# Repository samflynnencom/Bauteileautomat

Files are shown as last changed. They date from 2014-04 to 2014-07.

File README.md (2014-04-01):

Bauteileautomat
===============

This project merges the three branches of the student project "Bauteileautomat", a component vending machine built by students of the university of applied sciences Karlsruhe.
We all know the problem of working on a specific project and suddenly you encounter a missing part. And often it is a pretty common part like a 47k resistor you forgot to restock. That's where our vending machine comes into play. the machine holds the most common components and offers them to the students on the cheap.

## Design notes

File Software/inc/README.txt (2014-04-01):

Die includes sind in zwei Ordner aufgeteilt:

Im Ordner "driverlib" befinden sich alle Definitionen, die benötigt werden, wenn man die TivaWare nutzt. Dort befinden sich auch einige Konstanten. Diese Konstanten benötigt man, wenn man eine Applikation entwickelt. Später kann man ein eigenes Includefile schreiben, in dem die gesamten Konstanten selbst definiert werden können (muss aber nicht).
----
Im Ordner "hardware" befinden sich alle Includes, die man benötigt um die Hardware auf dem Chip selbst anzusprechen. Das bedeutet, wenn man den ADC nutzen möchte, dann benötigt man die Datei hw_adc.h dazu.
---

Normalerweise liefern die Dateien im Ordner "driverlib" die Konstanten wie auch Funktionsprototypen und die im Ordner "hardware" liegenden Includes die Definitionen zur eigentlichen Hardware. Die Tiva CPUs haben allerdings auch die Möglichkeit, die TivaWare, die in ihrem ROM steckt direkt zu nutzen. Dafür muss man vor alle Funktionen der TivaWare ein "ROM_" setzen und die include "rom.h" aus dem Ordner "driverlib" einbinden. Damit kann man allerdings ausschließlich Libraryfunktionen aus dem ROM nutzen. Wenn man sowohl Funktionen im Flash als auch im ROM nutzen möchte (zum Beispiel beim entwickeln), dann sollte man zusätzlich noch die Datei "rom_map.h" einbinden, die die Funktionen, die man als ROM_ nutzt, ersatzweise auf die Funktionen im Flash mappt.

Grundsätzlich gilt: Will man hardware ansprechen, bindet man die entsprechende hw_* aus dem Ordner "hardware" ein und sollte auch die entsprechende Funktion aus der Driverlib einbinden, gegen die man später linkt.

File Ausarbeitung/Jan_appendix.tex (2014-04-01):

\section{Anhang Elektronik}

\begin{figure}[h]

\hspace{-54pt}
\caption{Schemazeichnung des Mikrocontrollers mit Pinbelegung, JTAG Header und Takterzeugung. }
\label{SchemMic}
\end{figure}

\begin{figure}[h]

\hspace{-54pt}
\caption{Schemazeichnung der Netzwerkanbindung mit Koppeltrafo}
\label{SchemNetwork}
\end{figure}

\begin{figure}[h]

\hspace{-54pt}
\caption{Schemazeichnung der Motortreiber in der Daisychain}
\label{SchemMotor}
\end{figure}

\begin{figure}[h]

\hspace{-54pt}
\caption{Schemazeichnung der Motortreiber in der Daisychain}
\label{Board}
\end{figure}

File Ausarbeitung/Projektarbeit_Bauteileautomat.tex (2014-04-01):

\documentclass{scrartcl}
\usepackage[utf8]{inputenc}
\usepackage[german]{babel} 
\usepackage[colorlinks=true,
        linkcolor=black,
        citecolor=black,
        filecolor=black,
        urlcolor=black,
        bookmarks=true,
        bookmarksopen=true,
        bookmarksopenlevel=3,
        plainpages=false,
        pdfpagelabels=true]{hyperref}
\usepackage[square, numbers]{natbib}
\usepackage{setspace}
\usepackage[a4paper,left=2cm,right=2cm,top=2cm,bottom=4cm]{geometry}
\usepackage{graphicx}
\usepackage{morefloats}
\usepackage{ulem}
\usepackage{units}
\usepackage{wrapfig}
\usepackage{amsmath}
\usepackage{tikz}
\usepackage{colortbl} %Matze
\usepackage{xcolor}		%Matze 
\usepackage{pdfpages} %Matze
\usepackage{picinpar} %Matze
\definecolor{hellblau}{rgb}{0.8,0.8,1}
\definecolor {hellgruen}{rgb}{0.5,1,0.8}
%\usepackage{minted}
\usepackage[section]{placeins}
\usepackage{listingsutf8}
%\usepackage{wrapfig}
%\usepackage{pdfpages}
%\nocite{*}

\lstdefinestyle{customc}{
  belowcaptionskip=1\baselineskip,
  breaklines=true,
  frame=L,
  xleftmargin=\parindent,
  language=C,
  showstringspaces=false,
  basicstyle=\footnotesize\ttfamily,
  keywordstyle=\bfseries\color{green!40!black},
  commentstyle=\itshape\color{purple!40!black},
  identifierstyle=\color{blue},
  stringstyle=\color{orange},
}

\lstset{escapechar=@,style=customc, extendedchars=\true,
    inputencoding=utf8/latin1}

\parindent0mm

\newcommand {\Ohm} {$\Omega\ $}

\bibliographystyle{alphadin}

\begin{document}
\title{Projektarbeit 'Bauteileautomat'}
\author{
	Jan Krüger  \\
	Friedrichstraße 24 \\
	75417 Mühlacker \\
	Mtkl Nr: 37032 \\
	\and 
	Gregor Süß \\
	August-Dürr Straße 9 \\
	76133 Karlsruhe \\
	Mtkl Nr: 36496 \\
	\and
	Matthias Weißhaar \\
	Strümpfelbacher Straße 184\\
	71384 Weinstadt\\
	Mtkl Nr: 30250\\
	}

\date{\today}

\maketitle
\newpage

\tableofcontents
\newpage
\onehalfspace
\section{Einführung}
\subsection{Aufgabenstellung}
Für die Bereitstellung von elektronischen Bauteilen für die Studierenden der Elektrotechnik ist ein Ausgabeautomat zu entwickelen und zu erstellen. Der Automat ermöglicht den Studenten der Fakultät EIT zu jeder Tageszeit den Zugriff auf Elektronikbauteile (für ihre Studienprojekte und für den privaten Gebrauch). Der Automat soll viele kleine Fächer enthalten, damit aus einem reichhaltigen Sortiment an Bauteilen ausgewählt werden kann. Die Auswahl der Bauteile kann am Automaten oder vorab per Intranet erfolgen. Vor der Ausgabe der Teile ist eine Authentifizierung mit dem Studentenausweis am Automaten erforderlich. Der Bauteilebestand und die Verrechnung der entnommenen Bauteile sollen über eine Datenbank protokolliert werden. 

\subsection{Einleitung}
Der (Zeit-)Aufwand, der für die Erfüllung der Aufgabenstellung erforderlich ist, übersteigt das zeitliche Pensum einer Projektarbeit um ein vielfaches. Daher wurde die Aufgabenstellung in einer Gruppe bearbeitet und in drei Teile aufgeteilt. Ein besonderes Augenmerk lag auf einer klaren Trennung der Bereiche, damit eine enge Zusammenarbeit zwischen den Gruppenmitgliedern erreicht werden konnte. Im Hinblick auf die Ziele der Projektarbeit
(Projektgruppen die voneinander abhängig sind, Arbeiten nach Pflichten- und Lastenheften, etc) erschien diese Vorgehensweise als die beste. Der Aufbau dieses Dokuments spiegelt die klare Trennung der Aufgabenbereiche wider. Es ist in die drei Bereiche Elektronik, Software und Mechanik gegliedert, die erst einmal für sich selbst stehen und zusammen die Gesamtheit der Projektarbeit darstellen. Ziel dieses Dokuments ist es, die Arbeit zu dokumentieren und dem Leser einen Ansatzpunkt zur Weiterentwicklung des Automaten zu geben. 

\subsection{Aufgabenverteilung}
\begin{itemize}
\item
Jan Krüger betreut den Bereich 'Elektronik'. Dieser Bereich beinhaltet die Konzeption, Entwicklung und den Aufbau der Steuerplatine, der Verkabelung des Automaten und das Testen der Komponenten. Weiterhin gehört die Absprache der Bedürfnisse für den mechanischen Aufbau mit dem Bereich 'Software' zu seinem Aufgabengebiet. 
\item
Gregor Süß betreut den Bereich 'Software'. Er ist zuständig für die Konzeptionierung und Programmierung des Automaten. 
\item
Matthias Weißhaar betreut den Bereich 'Mechanik'. Dieser Bereich beinhaltet die Konzeption, Entwicklung und den Aufbau der mechanischen Komponenten, wie auch den Funktionstest derselben. 
\end{itemize}

\newpage

\section{Mechanik}
\label{Mechanik}
Dieses Kapitel dokumentiert die mechanische Funktionsweise und die Berechnung der zugehörigen Komponenten. Der Automat soll ca. 1000 Boxen enthalten, um eine große Auswahl zu gewährleisten. Damit dies in einer kompakten Bauweise möglich ist, werden drei unterschiedlich große Boxen verwendet. Die Boxen befinden sich in verschiedenen Schächten. 
Ein Schacht besteht aus jeweils zwei L-Profilen, die mit Schrauben an den Aluminiumprofilen der Rückwand befestigt werden. Die Größe der Schächte ist jederzeit änderbar und somit für jede Boxengröße variabel einstellbar. Ein Greifer, der auf X-Y-Z-Achsen verschiebar ist, fährt den ausgewählten Schacht an und greift anschließend die entsprechende Box. An der Seite des Automaten ist ein Rutsche angebracht, die zur Ausgabe der Teile dient. Der Greifer fährt diese an und kann durch ein Drehgelenk die Box um $180^\circ$ drehen und das gewünschte Teil auswerfen.

\subsection{Greifer}

\subsubsection{Anforderungen}

Der Greifer hat den sicheren Transport der Boxen zwischen den Schächten und der Rutsche zu gewährleisten. Er muss ein Drehgelenk beinhalten, das sich um $180^\circ$ drehen lässt. Weiter sind vom Greifer zwei verschieden große Boxen mit einem maximalen Gewicht von 1000g zu befördern. Damit die Ausgabe der Teile nicht zu lange dauert, muss die Geschwindigkeit des Greifvorgangs entsprechend hoch sein.

\subsubsection{Realisierung des Greifers}

Der Greifmechanismus erfolgt über zwei 20cm lange Greifarme aus Aluminium, wobei ein Greifarm fest verbaut ist und der andere über eine Trapezgewindespindel verfahrbar ist. Für den Antrieb der Spindel werden zwei Zahnräder verwendet, welche mit einem Schrittmotor verbunden sind. Damit der bewegliche Greifarm nicht verkantet, wird er über eine zusätzliche Welle geführt. Moosgummi auf dem Greifarm erhöht die Haftkraft zwischen den Boxen und den Greifarmen. Der Drehmechanismus erfolgt ebenfalls über zwei Zahnräder und einen Schrittmotor. Ein Zahnrad ist auf einer Welle befestigt, die auf einer Seite fest mit dem Greifer verbunden ist und auf der anderen Seite in einem Rillenkugellager gelagert ist. Durch das zweite Zahnrad, das durch einen Schrittmotor angetrieben ist, kann die Welle  mit dem Greifer rotiert werden. 

\subsubsection{Antrieb}

Alle relevanten Eigenschaften(Presskraft, Verfahrensgeschwindigkeit und Schrittlänge) sind abhängig vom Schrittmotor 
des Greifmechanismus. Für die richtige Dimensionierung des Schrittmotors sind entsprechende Berechnungen erforderlich.

\begin{itemize}

\item Haltekraft des Greifarms

Das Drehmoment des Motors muss den sicheren Transport einer Box mit einem Gewicht von 1000g gewährleisten. Zur Berechnung des Drehmoments wird die Presskraft benötigt, die der dynamische Greifarm auf die Box ausübt. Hier handelt es sich um einen Erfahrungswert, da verschiedene Berechnungsvariablen (z.b. Reibunkskoeffizent von Polystrol und Moosgummi) nicht vorhanden sind. Der Wert wurde daher auf $F=50N$ ausgelegt und bewußt höher gewählt, damit die Boxen auch bei kleinen Stößen und Vibrationen nicht aus dem Greifarmen rutschen können.\\
\newline

Durch die Umwandlung von einer Drehbewegung in eine Längsbewegung entsteht ein Wirkungsgrad, welcher durch den 
Steigungswinkel des Trapezgewindes und den Gewindereibungswinkel berechnet werden kann.\\

Den Steigungswinkel erhält man durch:

\[tan(\alpha)=\dfrac{P}{d\cdot \pi}=\dfrac{20mm}{4mm\cdot \pi}=\dfrac{5}{\pi}\]

\begin{tabbing}
mit \= P: Spindelsteigung\\
    \> d: Spindelnenndurchmesser  \\
		\> $\alpha$: Steigungswinkel\\
\end{tabbing}

Für ISO-Trapezgewinde mit geschmierter Mutter und einem Reibwert von $\mu=0.04$ erhält man den Gewindereibungswinkel mit:

\[ \rho=\mu\cdot 1.07= 0.04\cdot 1.07=0.043 \]

\begin{tabbing}
mit \= $\rho$: Gewindereibungswinkel\\
    \> $\mu$: Reibwert  \\
\end{tabbing}

Mit dem Steigungswinkel und dem Gewindereibungswinkel kann nun der Wirkungsgrad berechnet werden:

\[\eta=\dfrac{tan(\alpha)}{tan(\alpha +\rho)}=\dfrac{tan(\dfrac{5}{\pi})}{tan(\dfrac{5}{\pi}+0.043)}=3.08\]

\begin{tabbing}
mit \= $\eta$: Wirkunsgrad \\
\end{tabbing}

Das Antriebsdrehmoment der Spindel ergibt sich aus der Presskraft, der Steigung und dem Wirkungsgrad des Trapezgewindes: \\

\[M=\frac{F\cdot P}{1000\cdot 2\pi \cdot \eta}=\frac{50N\cdot 4mm}{1000\cdot 2\pi \cdot 3.08}=0.01Nm\]
\newline

\begin{tabbing}
mit \= M: Antriebsmoment\\
    \> F: Presskraft \\
\end{tabbing}

Auf das Ergebnis müssen die Verluste durch die Lagerung und der Wirkungsgrad der Übersetzung aufgeschlagen werden. Zur Berücksichtigung  dieser Verluste sollte die ausgewählte Leistung des Antriebs um 60\% bis 100\% über dem errechneten Wert liegen.\\

Mit dem Übersetzungsverhältnis der Zahnräder und den Verlusten des Greifmechanismus erhält man das geforderte Drehmoment des Motors durch:

Übersetzungsverhältnis der Zähnrräder:\\
\[i=\frac{z_2}{z_1}=\frac{30}{60}=0.5\]	

das Antriebsmoment des Schrittmotors:\\		
		
\[M_{Motor}=M_{Spindel}\cdot i \cdot R=0.01Nm \cdot 0.5 \cdot 1.6= 8Nmm \]

\begin{tabbing}
mit \= i: Übersetzungsverhältnis\\
    \> R: Reibungsverluste \\
\end{tabbing}

\item Schrittlänge

Die Schrittlänge ist der kleinstmögliche Weg, den der Greifarm zurücklegen kann. Bei einem Schritt des Motors wird dieser Weg zurückgelegt. Alle anderen Wege ergeben sich als ein vielfaches der Schrittlänge. Das weiche Moosgummi auf den Greifarmen und die Elastizität der Boxen erfordern eine feine Abstimmung der Presskraft der Greifarme. Für eine anwendungsgerechte Einstellung ist eine kleine Schrittlänge erforderlich.
\newpage

Mit dem Übersetzungsverhältnis kann die Schrittlänge des Greifers berechnet werden:
\[S=\frac{P}{\frac{360^\circ}{\alpha}}\cdot i=\frac{4mm}{\frac{360^\circ}{1.8^\circ}}\cdot 0.5=0.01mm\]

\begin{tabbing}
mit \= $\alpha$: Schrittwinkel des Elektromotors\\
    \> P: Steigung der Trapezgewindespindel
\end{tabbing}

Die geringe Schrittlänge ist ausreichend um die benötigte Presskraft einzustellen. Toleranzen des Gewindes oder der Schritte des Schrittmotors können vernachlässigt werden.
\newline

\item Geschwindigkeit des Greifarms\\

Um einen Schacht anzufahren müssen die Greifarme schon in der richtigen Schachtgröße positioniert werden. 
Die Positionierung findet während der Anfahrt an die jeweiligen Schächte statt. Somit muss nur noch das tatsächliche Greifen in einem gesonderten Arbeitsgang stattfinden. Hier ist der Verfahrensweg so klein $s<5mm$, dass die Geschwindigkeit größtenteils irrelevant ist. 

\end{itemize}

\subsubsection{Kugellager}

Um das Kugellager richtig zu wählen und eine lange Lebensdauer zu garantieren, wird die nominelle Lebensdauer nach 
ISO 281 berechnet:\\

\[L_{10h}=(\frac{C}{P})^p=(\frac{627N}{10N})^3 = 246492\]	

\begin{tabbing}
mit \= p: Lebensdauerexponent (bei Kugellager p=3)\\
    \> C: Dynamische Tragzahl in Kn(aus Lagertabelle des Herstellers) \\
    \> P: Dynamische äquivalente Belastung\\
		\> $L_{10}$: Lebensdauer in Millionen Umdrehungen bei 10\% Ausfallwahrscheinlichkeit
\end{tabbing}

Die nominelle Lebensdauer gibt an, wieviele Umdrehungen $90\%$ der Lager erreichen oder überschreiten bis die ersten Anzeichen von Werkstoffermüdung auftreten. Mit mehreren Millionen Umdrehungen bei 10\% Ausfallwahrscheinlichkeit ist für unsere Lager eine hohe Lebensdauer zuerwarten. Das Lager darf nicht zu groß dimensioniert werden, da ansonsten die Belastung der Lager zu gering wäre und kein Rollen der Wälzlager sondern Gleiten stattfindet. Gleitreibung sorgt für höheren Verschleiß und verkürzt daher die Lebensdauer.\\

Eine Lebensdauerberechnung ist für unsere Anwendung überflüssig, da die Kugellager nur sehr kleine Kräfte aufnehmen.
Zur Vervollständigung wurde diese jedoch trotzdem durchgeführt.

\subsubsection{Antrieb und Übersetzung Drehgelenk}

Das Drehgelenk wird ebenfalls über einen Schrittmotor angetrieben. Da hier nur eine Drehung von $180^\circ$ verlangt wird und der Motor ein hohes Drehmoment benötigt, wurde bei den Zahnrädern eine Übersetzung eingebaut.\\

Übersetzungsverhältnis der Zähnrräder:
\[i=\frac{z_2}{z_1}=\frac{14}{70}=0.2\]	

\begin{tabbing}
mit \= $z_1$: Zähnezahl\textsubscript{1} \\
    \> $z_2$: Zähnezahl\textsubscript{2} \\
\end{tabbing}

Durch das Übersetzungsverhältnis von 0.2 kann nun ein kleinerer Schrittmotor verwendet werden, dieser benötigt jedoch für eine Umdrehung die 5-fache Schrittanzahl. Auch hier müssen wieder Verluste eingerechnet werden und der Motor muss entsprechend größer dimensioniert werden.\\

Das Drehmoment berechnet sich zu:

\[M=F\cdot s\cdot i\cdot R = 10N\cdot  70mm\cdot 0.2\cdot 1.6 = 22.4Ncm\]

\begin{tabbing}
mit \= i: Übersetzungsverhältnis\\
    \> R: Reibungsverluste \\
		\> s: Länge(Kugellager-Greiferarm)\\
		\> F: Gewichtskraft des Greifers\\
\end{tabbing}

\subsubsection{Kugellager Drehgelenk}

Für die Ausgabe eines Bauteils rotiert das Kugellager $180^\circ$ und anschließend wieder $180^\circ$ zurück. Da nur eine Umdrehung pro Ausgabe am Kugellager notwendig ist, muss keine nominelle Lebensdauer für das Kugellager ausgerechnet werden. Es ist trotzdem wichtig, dass unser Kugellager mit einer mittleren Belastung betrieben wird. Das Verhältnis von dynamischer Tragzahl zu dynamischer äquivalenter Belastung sollte somit zwischen 8 und 15 liegen. Das Kugellager wird durch das komplette Gewicht von Greifer und Box radial belastet, welches mit 5kg ausgelegt wird. Eine axiale Belastung erfährt der Greifer nur durch die Beschleunigung der Z-Achse, welche hier gering ausfällt und somit vernachlässigt werden kann. 

\subsection{Achsen}

\subsubsection{Anforderungen X-Y-Z-Achse}

Um eine hohe Auswahlmöglichkeit im Automaten zu erreichen, muss dieser möglichst viele Boxen enthalten. Deshalb ist die größtmögliche Anzahl an Schächten im Automaten unterzubringen. Die L-Profile, welche die Schächte bilden, müssen sehr eng aneinander gereiht werden. Das Spiel zwischen den Schächten ist somit sehr gering und die Achsen müssen die jeweiligen Schächte präzise anfahren. \\
Die Ausgabezeit des Produktes ist für den Kunden wichtig und muss berücksichtigt werden. Damit der Kunde nicht zu lange auf sein gekauftes Bauteil warten muss, sind Verfahrensgeschwindigkeit und Beschleunigung der Achsen ebenfalls zu berücksichtigen und richtig zu dimensionieren. \\
Die Achsen müssen platzsparend im Automaten untergebracht werden und dürfen die Maße des Automaten nicht unnötig
vergrößern. Da die Verfahrenswege der Achse unterschiedlich lang sind, müssen die Berechnungen einzeln stattfinden. 
Der Automat soll eine lange Lebensdauer erreichen.\\

\subsubsection{Realisierung der Achsen}

Für den Vorschub der Achsen wurden Kugelumlaufspindeln verwendet, die jeweils mit zwei Linearführungen ein 
Linearmodul bilden. Die zwei Profilschienenführungen tragen die Masse des Greifmechanismus und garantieren die Einhaltung der linearen Bewegungsrichtung. Die Kugelumlaufspindel hat eine geringe Schrittlänge, welche sich im $\mu m$ Bereich einreiht, was für den Bauteileautomat ausreichend ist. Durch die geringe Reibung der Kugelumlaufspindel wird ein hoher Wirkungsgrad der Motoren und geringer Verschleiß erreicht, was zu einer hohen Lebensdauer der Achsen führt. Die Positioniergenauigkeit der Kugelumlaufspindel ist hoch und entspricht den Anforderungen unseres Automaten.\\

\begin{figure}[htbp] 
  \centering
     
			\caption{Z-Achse}
  \label{fig:Bild1}
\end{figure}

Der Antrieb der Achsen erfolgt über einen Schrittmotor, welcher über eine Oldham-Kupplung mit der Welle verbunden ist.
Die Kupplung überträgt das Drehmoment des Motors an die Welle und kann geringe parallele Versätze ausgleichen, die durch Fertigungsfehler entstehen können.\\

\subsubsection{Antriebsmoment der Z-Achse}

Die Bewegung der Z-Achse muss, wie der Greifmechanismus, getrennt von den anderen Bewegungen stattfinden. Die Beschleunigung und Verfahrensgeschwindigkeit darf daher nicht zu gering ausfallen. Trotz Reibung und Wirkungsgrad der Kugelumlaufspindel muss das Antriebsmoment des Schrittmotors so gewählt werden, dass eine akzeptable Verfahrenszeit erreicht werden kann.

\begin{itemize}

\item \textbf{Reibungskraft}

Die Reibungskraft, die in den Linearführungen auftritt, kann mit der folgenden Formel berechnet werden:

\[F_R=\mu\cdot m\cdot g+f=0.003 \cdot 5kg \cdot 9.81\dfrac{m}{s^2}+5N = 0.1N + 5N = 5.1N\]

\begin{tabbing}
mit \=$\mu$: Dynamischer Reibungskoeffizent\\
		\>m: Masse des Greifers\\
		\>g: Erdbeschleunigung\\
		\>f: Dichtungsbeständigkeit\\
\end{tabbing}

Aus der Rechnung ist ersichtlich, dass die Masse des Greifers kaum eine Rolle auf die Reibungskraft hat. 
Der Großteil der Reibung entsteht durch die verschiedenen Dichtungselemente der Linearführung (z.b. Dichtungslippe), 
welche nicht von der Last abhängig sind.

\item \textbf{Beschleunigung}
 
Der maximal verfahrbare Weg der Z-Achse beträgt $s=186mm$. Die Hälfte dieses Weges soll in einer Zeit von maximal $t=3s$ zurückgelegt werden. Somit ist auch gegeben, dass die Z-Achse auf der anderen Hälfte wieder gebremst werden kann. 

\begin{tabbing}
Beschleunigung: \qquad \=$\ddot{x}_a=a$\\
Geschwindigkeit: 							\>$\dot{x}_v=a\cdot t$\\
Verfahrensweg:												\>$x_s=0.5\cdot a\cdot t^2$\\
\end{tabbing}

Aus dem Verfahrensweg und der Zeit ergibt sich eine konstante Beschleunigung von:

\[a=\dfrac{2\cdot s}{t^2}=\dfrac{2\cdot 93mm}{9s^2}= 21\dfrac{mm}{s^2}\]

Die notwendige Kraft für die Beschleunigung erhält man aus der Masse des Greifers:

\[F_a=m\cdot a=5kg \cdot 0.021\dfrac{m}{s^2}=0.11N\]

\item \textbf{Antriebsmoment}

Mit der Reibungskraft, der notwendigen Kraft für die Beschleunigung und einem Wirkungsgrad von $\eta=0.9$ der Kugelumlaufspindel kann nun das erforderliche Antriebsmoment berechnet werden: 

\[M=\dfrac{(F_R + F_a) \cdot P}{2\pi \cdot \eta}=\dfrac{(5.1N+0.11N)\cdot 4mm}{2\pi \cdot 0.9}= 3.69Nmm\]

\begin{tabbing}
mit \=$F_R$: Reibungskraft\\
		\>$F_a$: Kraft für Beschleunigung\\
		\>P: Steigung Kugelumlaufspindel\\
		\>$\eta$: Wirkungsgrad Kugelumlaufspindel\\
		
\end{tabbing}

Auch hier müssen noch die Verluste durch die Lagerung der Kugelumlaufspindel hinzugerechnet werden. Zusätlich sollte noch 
eine Sicherheit mit eingerechnet werden. Insgesamt sollte das Antriebsmoment um das 1.5fache erhöht werden.

\[M_{Schrittmotor}=M \cdot 1.5 = 3.69Nmm \cdot 1.5 = 5.54Nmm\]

Der gewählte Schrittmotor muss somit ein Drehmoment von mindestens $M_{Schrittmotor} = 5.5Nmm$ aufweisen.

\end{itemize}

\newpage

\subsubsection{Linearführung Z-Achse}

\begin{itemize}

\begin{figure}[htbp]
	% minipage mit (Blind-)Text
	\hspace{10mm}
	\begin{minipage}[c]{0.5\textwidth} 

\item \textbf{Momente$(M_A/M_B/M_C)$}	\\
\newline
Die zulässigen statischen Momente der Linearführungen dürfen nicht überschritten werden, damit ein sauberer Lauf und eine lange Lebensdauer garantiert wird. Zudem wird eine Sicherheit von 3 eingebaut, damit Mehrbelastungen durch
dynamische Bewegungen nicht zu einer Überlast führen. Die statischen Momente $M_B$ und $M_C$ sind nicht vorhanden oder sehr gering und können vernachlässigt werden. Das kritische Moment $M_A$ ergibt sich durch die Gewichtskraft des Greifers und der Länge des Greifers. Das Moment wird auf zwei Linearführungen aufgeteilt und muss eine Sicherheit beinhalten.
	% \caption{Der Text}
	% \label{Text}
	\end{minipage}
	% Auffüllen des Zwischenraums
	\hfill
	% minipage mit Grafik
	\begin{minipage}[c]{0.4\textwidth}
	% \textwidth bezieht sich nun auf die Minipage
	
	\caption{Momente}
	\end{minipage}

\end{figure}

\[M_A>\dfrac{m\cdot g \cdot l \cdot s}{2}=\dfrac{5kg\cdot 9.81\dfrac{m}{s^2}\cdot 0.1m\cdot 3}{2}=7.5Nm\]

\begin{tabbing}
mit \=m: Masse\\
		\>g: Erdbeschleunigung\\
		\>l: Länge\\
		\>s: Sicherheit\\
\end{tabbing}

Das zulässige statische Moment der beiden Linearführungen muss mindesten 7.5Nm betragen.\\

\item \textbf{Nennnutzungsdauer}

Die Nennnutzungsdauer gibt den Verfahrensweg an, den $90\%$ der Linearführungen desselben Typs unter identischen 
Bedingungen zurücklegen können ohne dabei Schäden zu erleiden. Die Linearführungen des Bauteileautomats werden unter 
fast perfekten Bedingungen betrieben (kein Schmutz, keine hohen Temperaturen, niedrige Last). Der Anspruch der Lebensdauer für den Bauteileautomat wird damit weit übertroffen und eine Berechnung wird überflüssig. Dies gilt auch für die X-Y-Achsen.
\newline

%BERECHNUNG NICHT NOTWENDI
%\[P=F + \dfrac{C_0}{M_C}\times (F \times L_r) + \dfrac{C_0}{M_A}\times (F\times L_p)\]

%\begin{tabbing}
%mit \=F: Gewichtskraft des Greifers\\
%		\>$C_0$: Statische Tragzahl\\
%		\>$M_A$: Zulässiges statisches Moment - Steigungsrichtung  \\
%		\>$M_C$: Zulässiges statisches Moment - Rollrichtung\\
%		\>$L_p$: Distanz (Führungswagen-Lasmittelpunkt in Steigungsrichtung)\\
%		\>$L_r$: Distanz (Führungswagen-Lasmittelpunkt in Rollrichtung)\\
		
%\end{tabbing}

%\[L=(\dfrac{C}{P})^3\cdot50=(\dfrac{5kN}{P})^3\cdot50\]

%\begin{tabbing}
%mit \=L: Nennnutzungsdauer\\
%		\>P: Nutzlast\\
%		\>C: Dynamische Tragzahl\\

%\end{tabbing}

\end {itemize}

\subsubsection{Kugelumlaufspindel der Z-Achse}

\begin{itemize}

\item \textbf{Zulässige Axiallast}
 
Eine Berechnung der zulässigen Axiallast ist für die X-Z-Achsen nicht notwendig. Die Axialkräfte (Beschleunigungskraft) sind zu gering, um die zulässige Axiallast zu überschreiten. 

%BERECHNUNG BEI DER Z_ACHSE nicht nötig
%\item \textbf{Zulässige Axiallast}

%Die zulässige Axiallast ist eine Maximallast, die einschließlich einer Sicherheitstoleranz vor dem 	Abknicken einer %Gewindewelle aufgebracht werden darf. Die maximale Greiferlast darf die zulässige Last nicht überschreiten und muss %überprüft werden.
	 		
%\[P=m\cdot \dfrac{d^4}{l^2}^\cdot 10^4=10\cdot \dfrac{7.8^4}{}\]

%\begin{tabbing}
%mit \=P: Zulässige Axiallast\\
%		\>m: Faktor basierend auf Lagerart\\
%		\>d: Kerndurchmesser\\
%		\>l: Abstand zwischen den Belastungspunkten\\
%\end{tabbing}

\item \textbf{Zulässige Drehzahl}

Die Zulässige Drehzahl der Kugelumlaufspindel wird durch die kritische Drehzahl festgelegt. Die kritische Drehzahl ist diejenige Drehzahl, bei der ein Kugelgewindetrieb Resonanzerscheinungen zeigt. Sie ist abhängig vom Nenndurchmesser, der Spindellänge sowie der Lagerungsart.\\

\[N_c=g\cdot\dfrac{d}{l^2}\cdot 10^7 (min^{-1}) = 15.1\dfrac{mm}{min} \cdot \dfrac{7.8mm}{185mm^2}\cdot 10^7 = 573 \dfrac{1}{s}\]

\begin{tabbing}
mit \=$N_c$: Kritische Drehzahl\\
		\>d: Spindel-Kerndurchmesser\\
		\>g: Faktor für Lagerart\\
		\>l: Eingespannte Spindellänge\\
		
\end{tabbing}

Die Drehzahl der Kugelumlaufspindel der Z-Achse wird weit unter der zulässigen Drehzahl betrieben und muss somit nicht berücksichtigt werden. Auch die X-Y-Achsen werden weit unter den zulässigen Drehzahlen betrieben.

\item \textbf{Nennnutzungsdauer}

Auch hier ist die Lebensdauer sehr hoch, da das Gewicht größtenteils von den Linearführungen getragen wird und auf unsere Kugelumlaufspindel kaum Kräfte wirken. Nur die Beschleunigungskraft wirkt axial auf die Spindel, diese ist jedoch so klein das eine Berechnung überflüssig wird. Dies gilt auch für die X-Achse.

\end{itemize}

\subsubsection{Berechnungen der X-Achse}

Die X-Achse ist für die horizontale Anfahrt der Schächte zuständig und muss mit ca. 1m Länge auch eine ausreichend 
hohe Geschwindigkeit und Beschleunigung aufweisen. Auch hier ist keine Hubkraft notwendig, da das gesamte Gewicht 
radial auf die Lineareinheit wirkt. 

\begin{itemize}

\item \textbf{Beschleunigung und Geschwindigkeit}

Die Berechnung der Z-Achse zeigt, dass die Beschleunigung kaum eine Auswirkung auf das Antriebsmoment hat. Somit kann die Beschleuningung vernächlässigt werden, da der Schrittmotor bewusst höher gewählt wird, um im Betrieb Spiel zu haben und ggbf. die Verfahrensgeschwindigkeit zu erhöhen.
%Unsere Steigung ist 2.5fach so hoch als bei der Z-Achse. Um diesen Wert ändert sich also auch unsere maximale %Geschwindigkeit. Durch einen Schrittmotor mit einer höheren Drehzahl kann die Geschwindigkeit ebenfalls vergrößert %werden, falls dies benötigt wird.

\item \textbf{Antriebsmoment}

Das Antriebsmoment der X-Achse folgt auf der gleichen Berechnung wie das Antriebsmoment der Z-Achse. Da die Masse der Z-Achse noch mitverschoben wird, ändert sich die Gewichtskraft. Zudem besitzt die Kugelumlaufspindel eine ander Steigung als die Z-Achse. Somit ergibt sich:

\[F_R=m \cdot g\cdot \mu + f=10kg\cdot 9.81\dfrac{m}{s^2}  \cdot 0.005 + 5N=5.5N\]

Das Antriebsmoment erhält man durch: 

\[M=\dfrac{F_R\cdot P}{2\pi \cdot \eta}=\dfrac{5.5N\cdot 10mm}{2\pi \cdot 0.9}=9.7Nmm\]

Aufgrund von Verlusten sollte auch hier der Motor höher dimensoniert werden.

\[M_{Schrittmotor}=M \cdot 1.5 = 9.7Nmm \cdot 1.5 = 14.6Nmm\]

\item \textbf{Durchbiegung der X-Achse}

Durch die Gewichtskraft der Z-Achse und des Greifers kann es zu einer Durchbiegung der X-Achse kommen. Die Durchbiegung muss berechnet werden und ggf. bei der Justierung des jeweiligen Schachtes berücksichtigt werden. Es wird die maximale Biegung der Aluminiumprofile berechnet, auf denen die X-Achse verläuft.\\
\newline

Die maximale Durchbiegung erhält man mit:\\

\[f=\dfrac{F\cdot l^3}{(48+\dfrac{29\cdot m}{l})\cdot E \cdot I} = \dfrac{5kg\cdot 9.81\dfrac{m}{s^2}\cdot 0.55m^3}{(48+\dfrac{29\cdot 47mm}{820mm})\cdot 70000\dfrac{N}{mm^2}\cdot 0.9cm^4} = 0.86mm\]

\begin{tabbing}
mit \=E: Elastizitätsmodul\\
		\>I: Flächenmoment\\
		\>l: Länge der X-Achse\\
		\>F: Gewichtskraft (Greifer, Z-Achse)\\
\end{tabbing}

\begin{figure}[htbp] 
  \centering
     
			\caption{Z-Achse}
  \label{fig:Bild1}
\end{figure}
	
Mit einer maximalen Durchbiegung von 0.86mm müssen die Anfahrtswege der Schächte individuell justiert werden und die Schritte der Schrittmotoren auf die jeweiligen Schächte angepasst werden. 

\end{itemize}

\subsubsection{Linearführung der X-Achse}

\begin{itemize}
\item \textbf{Momente$(M_A/M_B/M_C)$}
%Bild einfügen Drehmomente

Die statischen Momente $M_B$ und $M_C$ sind nicht vorhanden oder sehr gering und können vernachlässigt werden. Das kritische Moment $M_A$ ergibt sich durch die Gewichtskraft des Greifers, die Gewichtskraft der Z-Achse und der Breite  des Greifers. Auch hier beinhaltet das Linearmodul zwei Linearführungen. Somit wird das Moment aufgeteilt und kann halbiert werden.

\[M_A>\dfrac{m\cdot g \cdot l \cdot s}{2}=\dfrac{10kg\cdot 9.81\dfrac{m}{s^2}\cdot 0.5m\cdot 3}{2}=29.5Nm\]

\begin{tabbing}
mit \=m: Masse\\
		\>g: Erdbeschleunigung\\
		\>l: Länge\\
		\>s: Sicherheit\\
\end{tabbing}

Das zulässige statische Moment der beiden Linearführungen muss mindesten 29.5Nm betragen.

\end {itemize}

\subsubsection{Berechnungen Y-Achse}

Für die Y-Achsen sind bestimmte Verfahrensgeschwindigkeiten erforderlich, da bei einer Länge von 1,7m die Anfahrtzeit des 
gewünschten Schachtes von Bedeutungung ist. Der Schrittmotor muss das Haltemoment und das Beschleunigungsmoment aufnehmen können. 

\begin{itemize}

\item \textbf{Beschleunigung und Geschwindigkeit}

Die Y-Achse soll die Hälfte ihrer Hublänge $s=0.85m$ in $t=2s$ verschieben. Das Antriebsmoment ist somit auch ausreichend um die Konstruktion in der anderen Hälfte der Hublänge wieder zum Stillstand zu bringen. Die maximale Verfahrenszeit der Y-Achse beträgt somit $t=4s$.

\begin{tabbing}
Beschleunigung: \qquad \=$\ddot{x}=a$\\
Geschwindigkeit: 							\>$\dot{x}=a\cdot t$\\
Hublänge:												\>$x=0.5\cdot a\cdot t^2$\\
\end{tabbing}

Aus der Hublänge und Zeit ergibt sich eine konstante Beschleunigung von:

\[a=\dfrac{2\cdot x}{t^2}=\dfrac{2\cdot 0.85m}{(2s)^2}=0.425\dfrac{m}{s^2}\]

\begin{tabbing}
mit \=x: Hublänge\\
		\>t: Zeit\\
\end{tabbing}

\item \textbf{Antriebsmoment}

Das erforderliche Antriebsmoment für den Schrittmotor ergibt sich aus dem Haltemoment und der benötigten Kraft der Beschleunigung. Da die gesamte Konstruktion durch zwei Y-Achsen angetrieben wird, teilt sich das Antriebsmoment auf die 
zwei Schrittmotoren auf und kann halbiert werden.\\

Die Kraft ergibt sich aus der zu tragenden Masse, welche auf 15kg ausgelegt wird (X-Achse, Z-Achse, Greifer, Box),
und aus den Beschleunigungen.

\[F=m\cdot (a+g)=15kg\cdot (0.425\dfrac{m}{s^2}+9.81 \dfrac{m}{s^2})=153.5N\]

Mit der Steigung der Kugelumlaufspindel, dem Wirkungsgrad und der Kraft erhält man das Antriebsmoment.

\[M=\dfrac{F\cdot P}{2\pi\cdot \eta}=\dfrac{153.5N\cdot 10mm}{2\pi\cdot 0.9}=271.5Nmm\]

\begin{tabbing}
mit \=a: Beschleunigung\\
		\>g: Erdbeschleunigung\\
		\>m: Masse\\
		\>P: Steigung Kugelumlaufspindel\\
		
\end{tabbing}

Auch hier muss eine Sicherheit von 20\% eingerechnet werden, da Verluste durch Lagerung und Reibung enstehen.   
Man erhält somit ein Antriebsmoment je Schrittmotor von:

\[M{M_{Schrittmotor}}=\dfrac{M\cdot \eta_{Verlust}}{2}=\dfrac{271.5Nmm\cdot 1.2}{2}=162.9 Nmm\]

\item \textbf{Rastmoment}

Das Rastmoment definiert das maximale Drehmoment, das am stromlosen Motor anliegen kann, ohne dass er sich dreht.
Dies ist besonders wichtig bei Stromausfall. Da die Kugelumlaufspindel keine Selbsthemmung besitzt würde die Y-Achse
nach unten stürzen. Durch das Rastmoment $M_{Rast}=0.068Nm$ der zwei Schrittmotoren könnte die Y-Achse abgebremst werden und nach einiger Zeit zum Stillstand kommen. Da die Masse des Greifers und der Achsen unter dem angenommenen Wert liegen wird und die Verluste nicht genau bestimmt werden können, muss dies noch im Betrieb getestet werden und möglicherweiße eine zusätliche Sicherheit bei Stromausfall eingebaut werden. 

\end{itemize}
\newpage
\subsubsection{Linearführung der Y-Achse}

\begin{itemize}
\item \textbf{Momente$(M_A/M_B/M_C)$}

Auch hier sind die statischen Momente $M_B$ und $M_C$ sind nicht vorhanden oder sehr gering und können vernachlässigt werden. Das kritische Moment $M_A$ ergibt sich durch die Gewichtskraft des Greifers, die Gewichtskraft der Z-Achse und X-Achse und der halben Länge der X-Achse. Durch die zwei Linearmodule mit jeweils zwei Linearführungen teilt sich das Moment auf die vier Schlitten der Linearführung auf.

\[M_A>\dfrac{m\cdot g \cdot l \cdot s}{4}=\dfrac{15kg\cdot 9.81\dfrac{m}{s^2}\cdot 0.5m\cdot 3}{4}=55.2Nm\]

\end{itemize}

\subsubsection{Kugelumlaufspindel der Y-Achse}

\begin{itemize}

\item \textbf{Zulässige Axiallast}

Die zulässige Axiallast ist eine Maximallast, die einschließlich einer Sicherheitstoleranz vor dem 	Abknicken einer Gewindewelle aufgebracht werden darf. Die Y-Achse ist senkrecht im Automaten eingebaut und wird daher stark axial belastet.
Somit muss die zulässige Axiallast überprüft werden und darf nicht überschritten werden.
	 		
\[P=m\cdot \dfrac{d^4}{l^2}^\cdot 10^4=10\dfrac{kg\cdot mm^2}{s^2}\cdot \dfrac{16.3^4mm^4}{1700^2mm^2}\cdot 10^4m=2.44kN\]

\begin{tabbing}
mit \=P: Zulässige Axiallast\\
		\>m: Faktor basierend auf Lagerart\\
		\>d: Kerndurchmesser\\
		\>l: Abstand zwischen den Belastungspunkten\\
\end{tabbing}

Jede Achse kann somit ein Axiallast von maximal 2.44kN aufnehmen. Dies ist ausreichend und wird nicht überschritten.

\end{itemize}

\subsection{Gestaltung des Rahmens}

Der Aufbau des Rahmens besteht aus Aluminiumprofilen. Diese bilden große Gestaltungsspielräume und einen schnellen Aufbau. Die Aluminiumprofile können nachträglich schnell demontiert werden und kleine Änderungen am Automaten sind ohne großen Aufwand zu realisieren. Die L-Profile der Schächte, welche auf die Aluminiumprofile montiert sind, können jederzeit verändert werden. Somit ist die Größe der Schächte sehr variabel. Sobald der Automat eine höhere Kapazität von großen Boxen benötigt, können die schmalen Schächte zu Breiten Schächten umgebaut werden und umgekehrt.\\

\begin{figure}
  \centering
     
			\caption{Schächte für die Lagerung der Boxen}
  \label{fig:Bild1}
\end{figure}

Der Automat ist mit Kunststoffplatten verkleidet. Um den Studenten die Funktionsweise des Automaten zu zeigen, wird an der 
Vorderseite ein Teil mit Plexiglas ausgefüllt. Zur Bedienung des Automaten befindet sich an der Vorderseite ein Touchscreen.  Die Bezahlung der entnommenen Teile erfolgt per Kartenlesegerät, welches noch nachträglich am Automat montiert wird. Rechts vom Automaten wird eine kleine Tür mit Schloss eingebaut. Somit kann der Automat schnell befüllt werden, ohne die Verkleidung abschrauben zu müssen. 

Unter der Tür befindet sich die Ausgabe, wo die Studenten die gekauften Teile entnehmen. Die gekauften Teile werden mit einer Rutsche zum Ausgabefach befördert.Die Elektronik befindet sich am Boden des Automaten. Der Greifer kann hier nicht hinfahren, da seitlich die Motoren der Y-Achse verbaut sind. Der Platz kann daher für die Elektronik benutzt werden.

\newpage
\subsection{Daten und Komponenten des Automaten}

Die wichtigsten Daten des Bauteileautomaten im Überblick:

\begin{tabbing}
\textbf{Grundmaße:} \quad    \=Die Grundmaße des Bauteileautomaten in Höhe, Breite und Tiefe\\
											  \>sind ca.: 2000mmx1000mmx7500mm\\
\textbf{Gewicht:}			  \>Das Gesamtgewicht des Automaten ohne Inhalt der Boxen beträgt ca. 75kg.\\
\textbf{Kapazität:}		  \>Der Automat kann ca. 1000 rote Boxen zur selben Zeit lagern.\\
\textbf{Ausgabezeit:}	  \>Der Automat braucht durschnittlich ca. 10s, um ein gewünschtes Teil zur Ausgabe\\
												\>zu befördern.\\

\end{tabbing}

Die Daten der drei verschiednen Boxen:
\newline
\newline
\begin{tabular}{l c l l}
\rowcolor{hellblau}
Farbe\qquad\qquad\qquad&\qquad\qquad Länge x Höhe x Breite\qquad\qquad& Gewicht\quad\qquad\qquad& Werkstoff\\
\hline
\colorbox{red}{ } rote Box&54  x  45  x  54& 0.1kg& Polystyrol (PS)\\
\hline
\colorbox{yellow}{ } gelbe Box&108  x  45  x  54& 0.22kg& Polystyrol (PS)\\
\hline
\colorbox{blue}{ } blaue Box&108  x  45  x  108& 0.35kg& Polystyrol (PS)\\
 
\end{tabular}
\newline

\subsubsection{X-Y-Z Achsen}

%Die Daten der X-Y-Z Achsen:\\

%\begin{tabular}{l l l l l l l}
%\rowcolor{hellblau}
%Achse& max. Geschwindigkeit& Gewicht& Drehmoment_z& Drehmoment_x& Drehoment_y& Länge\\
%\hline
%Z-Achse&Wert&Wert&Wert&Wert&Wert&Wert\\
%\hline
%X-Achse&Wert&Wert&Wert&Wert&Wert&Wert\\
%\hline
%Y-Achse&Wert&Wert&Wert&Wert&Wert&Wert\\
 
%\end{tabular}
%\newline
%\newline
%Die Berechnungen der jeweiligen Daten können in den oberen Abschnitten des Berichtes nachvollzogen werden.
%\newline
%\newline 
Die zugehörigen Komponenten der X-Y-Z Achsen:
\newline

\begin{tabular}{l l l l l}
\rowcolor{hellgruen}
Achse&Gewindetriebe&Kupplung&Linearführungen&Motor\\
\hline
Z-Achse&BSSC1004-280-SWC5&MCO15-5-6&SSVR24-280&PSM42BYGHW603\\
\hline
X-Achse&BSSC1510-835-SWC7&MCO20-6.35-10&SVRN28-820&ST5918X1008\\
\hline
Y-Achse&BSSC2010-1670-SWC7&MCO20-6.35-12&SVRL28-1700&ST5918L1008\\
\newline
\newline
\end{tabular}

\begin{tabular}{l l l l l l l l}
\rowcolor{hellgruen}
Achse&Führungswagen&Loslager&Festlager\\
\hline
Z-Achse&BNFA1004C-30&BUV8&BSV8S\\
\hline
X-Achse&BNFA1510C-30&BUV12&BSV12\\
\hline
Y-Achse&BNFA2010C-30&BUV15&BSV15\\
\newline
\newline
\end{tabular}

Alle Komponenten für die Achsen sind von \textsl{MiSUMi}. Die verschiedene Maße und die technischen Eigenschaften der einzelnen Komponenten  können im Anhang oder unter \url{www.misumi-europe.de} nachgeschlagen werden.

\subsubsection{Greifarm}

Komponenten des Greifarms:\\
\newline
\begin{tabular}{l| l l l l l l l l l}
\rowcolor{hellgruen}
 &Festlager&Loslager&Motor&$Zahnrad_1$&$Zahnrad_2$\\	%Zahnrad_1 = Zahnrad_Motor
\hline
Greifmechanismus&16002&N202-E-TVP2&PSM42BYGHW603&416-010-0022&416-010-0066\\
\hline
Drehglenk&16002&nicht vorhanden&PSM42BYGHW603&416-010-0014&416-010-0070\\
\end{tabular}
\newline
\newline

\begin{tabular}{l| l l l l l l l l l}
\rowcolor{hellgruen}
 &Mutter&Trapezgewinde&Welle&Linearkugellager\\	%Zahnrad_1 = Zahnrad_Motor
\hline
Greifmechanismus&MTSPNR20&MTSRX20&PSFRM12&LMK12\\
\hline
Drehglenk&nicht vorhanden&nicht vorhanden&nicht vorhanden&\\
\end{tabular}
\newline
\newline
Die Komponenten für den Greifarm wurden teilweise in der Elektrotechnikwerkstatt gefertigt. Verschiedene Maße und
technische Eigenschaften sind aus den technischen Zeichnungen oder aus der CAD-Datei zu entnehmen. Die restlichen Komponenten wurden bei \textsl{MiSUMi} bestellt (\url{www.misumi-europe.de}), \textsl{G\&G Antriebstechnik} (\url{www.gg-antriebstechnik.de}), \textsl{ekugellager} (\url{www.ekugellager.de}), \textsl{Pollin} (\url{www.pollin.de}) und \textsl{Nanotec} (\url{www.de.nanotec.com}) bestellt. Wichtige technische Größen und Maße können auf der angegebenen Homepage nachgeschlagen werden oder den angehängten Datenblättern entnommen werden.

\subsection{Schmierung/Instandhaltung}

Um einen ruhigen Lauf des Automaten zu garantieren, müssen die Kugelumlaufspindeln, Linearführungen und Kugellager geschmiert werden. Somit wird die Reibung minimiert und eine maximale Lebensdauer der Komponenten erreicht. Auch ohne Schmutzeinwirkung ist eine einmalige Lebensdauerschmierung erfahrungsgemäß nicht ausreichend. Es sollte regelmäßig eine Kontrolle der Schmierung stattfinden und ggf. eine Nachschmierung erfolgen.

\subsection{Quellenangabe}

\url{www.misumi-europe.de}\\
\url{www.gg-antriebstechnik.de}\\
\url{www.gg-antriebstechnik.de}\\
\url{www.ekugellager.de}\\
\url{www.pollin.de}\\
\url{www.de.nanotec.com}\\
\url{www.wikipedia.de}\\
Tabellenbuch Metall

\newpage

%%%%%%%%%%%%%%%%%%%%%%%%%%%%%%%%%%%%%%%%%%%%%%%%%%%%%%%%%%%%%%%%%%%%%%%%%%%%%%%%%%%%%%%%%%%%%%%%%%%%%%%%%%%%%%%%%%%%%%%%%%%%%%%%%%%%%%%%%%

\section{Elektronik}
\subsection{Anforderungen an die Elektronik}
In Kapitel \ref{Mechanik} wurde die Funktionsweise des Automaten beschrieben. Daraus ergaben sich die Anforderungen an die zu entwerfende Elektronik. In Abbildung \ref{BlockDiag} ist eine Übersicht der Komponenten abgebildet. Als Kommunikationsschnittstelle wurde das SPI\footnote{Serial Peripheral Interface, von Motorola entwickelt} genutzt, da das Interface eine schnelle Datenübertragung bei einer relativ kleinen Anzahl von benötigten Pins (Im Gegensatz zu parallelen Interfaces) ermöglicht. Weiterhin haben die meisten Controller Peripherie, die entweder direkt eine SPI Schnittstelle ist oder zumindest eine SPI-kompatible Schnittstelle bereitstellt.

\begin{figure}[h!]
\begin{center}
\begin{tikzpicture}[>=stealth]
  %coordinates
  \coordinate (orign)  at (0,0);
  \coordinate (ETHBox) at (0,6);
  \coordinate (UARBox) at (0,0);
  \coordinate (CPUBox) at (5,3);
  \coordinate (IDev)   at (5,0);
  \coordinate (ODev)   at (5,6);
  \coordinate (Power)  at (0,3);
  \coordinate (MCont1) at (10,6);
  \coordinate (MCont2)    at (10,3);
  \coordinate (MCont3)    at (10,0);

  %nodes
  \node[draw, minimum width=3.3cm, minimum height=2cm, anchor=south west, text width=3cm, align=center] (A) at (ETHBox) {Ethernet \\ Communication};
  \node[draw, minimum width=3.3cm, minimum height=2cm, anchor=south west, text width=3cm, align=center] (B) at (UARBox) {UART \\ Communication};
  \node[draw, minimum width=3.3cm, minimum height=2cm, anchor=south west, text width=2cm, align=center] (C) at (CPUBox) {$\mu$C};
  \node[draw, minimum width=3.3cm, minimum height=2cm, anchor=south west, text width=2cm, align=center] (D) at (IDev) { Human Input};
  \node[draw, minimum width=3.3cm, minimum height=2cm, anchor=south west, text width=2cm, align=center] (E) at (ODev) {Display};
  \node[draw, minimum width=3.3cm, minimum height=2cm, anchor=south west, text width=2cm, align=center] (F) at (Power) {Spannungs- \\ versorgung};
  \node[draw, minimum width=3.3cm, minimum height=2cm, anchor=south west, text width=2cm, align=center] (G) at (MCont1) {Motor \\ Controller};
  \node[draw, minimum width=3.3cm, minimum height=2cm, anchor=south west, text width=2cm, align=center] (H) at (MCont2) {...};
  \node[draw, minimum width=3.3cm, minimum height=2cm, anchor=south west, text width=2cm, align=center] (I) at (MCont3) {Motor \\ Controller};

\draw[<->] (A) edge node[above right,pos=0.5] {SPI} (C);
\draw[<->] (B) edge node[below right, pos=0.5] {SPI} (C);
\draw[<->] (D) edge node[auto] {SPI} (C);
\draw[<->] (E) edge node[auto] {SPI} (C);
%%\draw[->]  (C) center node[auto] {SPI} (G);
\draw[->] (C) edge node[below right] {SPI} (G);
\draw[->] (G) edge node[auto] {SPI} (H);
\draw[->] (H) edge node[auto] {SPI} (I);
\draw[->] (I) edge node[below left] {SPI} (C);

%TODO: Inputs und Outputs müssen noch bepfeilt werden. 

\end{tikzpicture}

\end{center}
\caption{Blockdiagramm der Komponenten und deren Beziehungen zueinander}
\label{BlockDiag}
\end{figure}

\newpage

\subsection{Spannungsversorgung}
Die Spannungsversorgung besteht aus zwei Teilen mit unterschiedlichen Anforderungen:
\begin{itemize}
\item{Spannungsversorgung des Digitalteils}
\item{Spannungsversorgung des Leistungsteils}
\end{itemize}
Die Spannungsversorgung des Digitalteils muss stabile 3,3V bei ca. 500mA liefern. Dabei muss beachtet werden, dass sich durch die Verbindung des Digital- und des Leistungsteils über die Motortreiber (Siehe Kapitel \ref{Motorcontroller}) eventuell Probleme mit der Spannungsstabilität ergeben und dadurch Bitfehler entstehen können. Um universell sein zu können sollte der Digitalteil zudem mit einem weiten Eingangsspannungsbereich versorgt werden können.  \newline

Zum Betrieb der Motorendstufen ist eine zweite, sehr niederohmige Quelle nötig. Diese Quelle wird durch ein plötzliches Anfahren von einem oder mehrerer Motoren gleichzeitig stark belastet und muss daher eine hohe Regelgeschwindigkeit aufweisen. Die ausgewählten Motortreiber (siehe Kapitel \ref{MotDriv}) ermöglichen einen effektiven Stromfluss von $I_{eff} = 3A$. Da der Automat über 5 Freiheitsgrade verfügt (Ein Freiheitsgrad wurde mit 2 Motoren realisiert um eine hohe Beschleunigung zu erreichen), fließt ein effektiver Gesamtstrom $I_{eff,gesamt} = 6*3A = 18A$. Der Spitzenstrom, der durch einen Treiber fließen kann (Treiberintern begrenzt), beträgt $I_{max} = 7A$. Die Spitzenlast beträgt also $I_{max,gesamt} = 6*7A = 42A$ wenn alle Treiber an ihrem Limit arbeiten. In der Praxis ist dieser Fall allerdings ausgeschlossen, da die Treiber erstens eine Limitierung des Stromes erlauben und zweitens wird ein Stillstand sofort detektiert und der entsprechende Treiber geht in den Fehlermodus. Ein Stillstand entspricht dem größten Lastfall für die Treiber, da der Strom lediglich vom ohmschen Widerstand der Motorspulen abhängt, der in der Größenordnung 1\Ohm bis maximal 10\Ohm liegt. Nicht zuletzt wurden die Motoren auch nach ihrer nominellen Stromaufnahme ausgewählt, um eine solche Überlast zu vermeiden. \newline

Von Anfang an war eine getrennte Spannungsversorgung von Steuerelektronik und Leistungselektronik vorgesehen. Von der Lösung wurde sich mehr Flexibilität im Bezug auf die Versorgungsspannung des Leistungsteils erhofft und gleichzeitig sollte die Maßnahme die Entwicklungszeit verkürzen, indem zwei verschiedene Netzteile genutzt werden konnten. Bei einer Versorgung aus eine gemeinsamen Quelle hätte sichergestellt werden müssen, dass die Induktivitäten der Motoren bei Lastspitzen (wie sie beim Anfahren mehrerer Motoren gleichzeitig entstehen) die Versorgung des Digitalteils nicht oder nur geringfügig stören. Eine Folge eines Abfalls der Versorgungsspannung ist zum Beispiel der Brownout\footnote{Als Brownout wird ein, aufgrund einer kurzzeitigen oder auch länger andauernde Verminderung der Versorgungsspannung, Zustand bezeichnet, bei der ein System nicht länger in der Lage ist, zuverlässig zu arbeiten. Aus diesem Grund besitzen die meisten modernen Mikrocontroller eine Brownout Detection, die den Controller über einen Reset wieder in einen definierten Zustand bringen. }. Um das Eintreten eines solchen Zustand zu verhindern benötigt man entweder relativ große Kondensatoren, die die Spannung bis zur Nachregelung durch das Netzteil konstant halten oder eine gute Filterung der Spannungsversorgung für den Digitalteil.\newline
Falls das verwendete Netzteil die Spannungsschwankungen gut ausregelt, ist es auch bei getrennten Versorgungsanschlüssen möglich, den Leistung- und den Digitalteil aus einer Quelle zu versorgen. \newline

Durch diese Überlegungen ergeben sich folgende Vorgaben für den Spannungswandler des Digitalteils: \newline
\begin{itemize}
\item{Eingangsspannungsbereich: 5-24 Volt}
\item{Ausgangsspannung: 3,3V}
\item{Strombelastbarkeit: 500 mA}
\item{Restwelligkeit kleiner 5mV}
\end{itemize}
Erreicht wurden diese Parameter durch eine Kombination des DC/DC Wandlers LT1376\footnote{Datenblatt: \url{http://cds.linear.com/docs/en/datasheet/13756fd.pdf} (Vom \today)}, der die Spannung auf etwa 4-5 Volt (je nach Toleranz der Feedbackwiderstände) heruntersetzt, und einem nachgeschalteten Festpannungsregler des Typs LT1763\footnote{Datenblatt: \url{http://cds.linear.com/docs/en/datasheet/1763fg.pdf} (Vom \today)}, welcher die Spannung auf die vorgegebenen 3,3 Volt heruntersetzt.

\begin{figure}[h]

\hspace{-14pt}
\caption{Schemazeichnung der Spannungsreglerbaugruppe mit Lastwiderstand am Ausgang.}
\label{ltspice}
\end{figure}
Über zwei parallel geschaltete 4,7$\mu$F Pufferkondensatoren (In Abbildung \ref{ltspice} sind das C2 und C5 mit 100$\mu$F) wird die Spannung über die Spule L1 und die Diode D2 herabgesetzt. D1 und C3 dienen zur Erzeugung der für den im LT1376 integrierten MOSFET nötigen Schaltspannung.
Für den Spannungsteiler R1 und R2, der die Feedbackspannung erzeugt, wurden handelsübliche Werte aus der E12 Reihe gesucht, die eine Spannung von etwas über 3,8 Volt am Ausgang des DC/DC Wandlers erzeugt, welche über C2 und C5 gesiebt und stabilisiert wird. Die Ausgangsspannung des DCDC Wandlers wurde durch Addition der geplanten Ausgangsspannung des Linearreglers plus dessen maximalem Dropout berechnet. Das Ausgangsnetzwerk besteht aus dem Stützkondensator C7 und dem Bypasskondensator C6. C6 dient normalerweise dazu das Rauschen des Reglers (Größenordnung 20$\mu$V) zu unterdrücken und wäre hier aufgrund der großen Spannungsrippel unnötig. Dennoch ist es eine gute Praktik ihn in das Schaltbild und die endgültige Schaltung zumindest als Option mit einzuplanen. Ob er im finalen Layout dann bestückt wird ist dem Entwickler überlassen. \newline
Um die Stromlieferfähigkeit zu überprüfen wurde die Baugruppe in LTSpice\footnote{Download: \url{http://www.linear.com/designtools/software/\#LTspice} (Vom \today)} mit einem Widerstand von 6,6$\Omega$ belastet und der Verlauf der Spannung über die Zeit aufgenommen. Dabei wurde eine Einschwingzeit von etwa 30ms abgewartet um der Baugruppe Zeit zu geben, sich auf die endgültige Spannung einzuschwingen.
\begin{figure}[h]

\hspace{-14pt}
\caption{Simulation der Ausgangsspannung im eingeschwungenen Zustand über die Zeit und Messung der Restwelligkeit.}
\end{figure}

In der Simulation sieht man, dass die geregelte Spannung mit 3,26 Volt und einer Restwelligkeit von unter 2mV bei etwa 500mA stabil ist. \newline

Der Aufbau des Spannungsreglers stellte sich allerdings als schwierig heraus. Es wurde davon ausgegangen, dass die Hochschule in der Lage ist, die meisten Bauteile zu löten. Daher wurden Widerstände, Optokoppler, etc per Hand gelötet und nur Mikrocontroller wie auch Motortreiber sollten mit Hochschulmitteln auf die Platine gelötet werden. Diese Annahme war allerdings falsch: es gestaltet sich schwer, QFN Bauteile wie den LT1763 auf die Platine zu bringen, da für QFN Bauteile mit Wärmeleitpad unter dem Chip ein Reflowofen benötigt wird. Ein Platzieren und Löten per Hand gestaltet sich aufgrund des Wärmeleitpads unterhalb des ICs und der sich daraus ergebenden Gefahr, Pins mit dem Pad zu verbinden, als schwer bis unmöglich. Daher wurde beschlossen, den LT1763 durch den bewährten Linearregler LT1117\footnote{Datenblatt: \url{http://cds.linear.com/docs/en/datasheet/1117fd.pdf} (Vom \today)} zu ersetzen, der rücklings auf eine freie Stelle der Platine geklebt wird und über Drähte mit dem Ausgang des ursprünglich geplanten Linearreglers zu verbinden. Die 4,7$\mu$F werden mit einer 10$\mu$F Kapazität gleicher Baugröße ersetzt, da der LT1117 im Gegensatz zu anderen Linearreglern einen größeren Kondensator benötigt.

\subsection{Mikrocontroller}

Zu Anfang der Projektarbeit war durch die relativ offen gestellte Aufgabenstellung noch nicht ganz klar, welche Rolle die Steuerelektronik spielen würde. Es gab mehrere Szenarien:
\begin{itemize}
\item{Die Steuerelektronik übernimmt die Motoransteuerung, Sortierung der Boxen, Ein- und Ausgabefunktionen, Bestand des Warenhaushalts, das Webinterface und die Verifikation des Studentenstatus beim Kauf von Hardware.}
\item{Die Steuerelektronik übernimmt die Motoransteuerung, Sortierung der Boxen und die restliche Ein- und Ausgabefunktionen. Darüber befindet sich eine 'höhere Logik' wie zum Beispiel ein Computer, der sich um die Lagerverwaltung und die Verifikation des Studentenstatus der Käufer kümmert.}
\item{Die Steuerelektronik übernimmt lediglich die Motoransteuerung und die Ein- und Ausgabefunktionen. Eine 'höhere Logik' übernimmt die komplette Bestandsverwaltung, die Überprüfung auf Studentenstatus und die Netzwerkfunktionalität.}
\end{itemize} 
Dadurch ergaben sich folgende Anforderungen an den Mikrocontroller:
\begin{itemize}
\item{Mindestens 3 Interfaces zur schnellen Anbindung von Peripherie, bevorzugt seriell}
\item{5V tolerante Eingänge um auch Hardware mit TTL Pegel ansteuern zu können}
\item{Handlötbares Package. Vorzugsweise 64LQFP, maximal 100LQFP.}
\item{Mindestens eine U(S)ART Schnittstelle}
\item{Bewährte, konsistente und 'Royality free' Funktionsbibliotheken bzw API}
\item{Integrierte FPU}
\item{Mindestens 32kB RAM}
\item{USB Device Port für zukünftige Erweiterungen}
\item{Genug Rechenleistung zur schnellen Auslieferung von Webseiten (Erfahrungswert etwa 50DMIPS)}
\end{itemize}
Mithilfe dieser Anforderungen wurde der TM4C123A6HPM als Mikrocontroller ausgewählt. Der $\mu$C gehört der Tiva C Serie an. Diese Serie wurde von Texas Instruments im Juli 2013 neu eingeführt und steht damit am Anfang ihres Lebenszyklus. Damit ist eine Verfügbarkeit über einen relativ langen Zeitraum gegeben. Weiterhin stellt der Mikrocontroller keine strikten Anforderungen an die Spannungs- und Taktversorgung was das Platinenlayout einfach macht. \newline
Ein weiteres Entscheidungskriterium waren die günstigen Evaluationsboard, die Texas Instruments zur Tiva C Serie zur Verfügung stellt. Diese wurden genutzt um den Mikrocontroller kennen zu lernen und die Firmware parallel zum Design der Elektronik entwickeln zu können.\newline

Abbildung \ref{SchemMic} zeigt die Grundbeschaltung des Mikrocontrollers. Da TI keine Library für das Layoutprogramm Eagle anbietet, wurde diese selbst erstellt, allerdings für den TM4C1233H6PM(I). Dieser hat jedoch das gleiche Pindiagramm wie der verwendete TM4C123A6HPM(I). In diesem Fall wurde mangels Hardware das im Chip integrierte ARM Debugwire nicht genutzt und auf JTAG als Programmier- und Debugschnittstelle gesetzt. Da der Controllertakt über eine PLL stabil gehalten wird, ist die Auswahl an Quarzen groß. Hier wurde ein 16MHz Quarz gewählt, da 16MHz Quarze noch Grundwellenquarze sind und somit relativ problemlos eingesetzt werden können, da sie im Gegensatz zu Oberwellenquarzen nur eine einfache Beschaltung benötigen. \newline
Der RESET Pin ist LOW-aktiv, muss im Betrieb also konstant auf HIGH gehalten werden. Um den Chip programmierbar zu machen, wird hier eine 10k$\Omega$ und 1nF RC-Kombination eingesetzt, die den IC nach dem Programmiervorgang nach lange genug im RESET Zustand hält. Erfahrungsgemäß benötigen manche Programmieradapter einen größeren Kondensator, da der RESET Pin bei hohen Programmiergeschwindigkeiten zu früh auf HIGH gesetzt wird, der Flash Speicher allerdings noch nicht fertig beschrieben ist. Wenn mit dem Programmer auf dem Evaluation Board programmiert wird, ist der 1nF Kondensator allerdings ausreichend. \newline
Alle Pins, die Betriebsspannung führen, wurden mit 100nF Stützkondensatoren gegen GND gepuffert um Stromspitzen abfangen zu können. Um die Platine debuggen zu können wurden zwei LEDs mit eingeplant, die zur Anzeige diverser Zustände verwendet werden können. Die LEDs sind so geschalten, dass der Controller den Pin gegen GND ziehen muss damit die entsprechende LED leuchtet. Die Art der Verschaltung dient dazu, den Ausgang nicht zu stark zu belasten: Die ARM GPIO Peripherie kann (wenn keine Peripherie vom Chiphersteller hinzugefügt wurde) maximal 8mA pro Pin sourcen, jedoch weitaus mehr sinken, also gegen GND ableiten.

\subsection{Digitale Eingänge} 

\begin{wrapfigure}{r}{0.5\textwidth}

\hspace{-14pt}
\caption{Digitaler Eingang}
\label{OptoKop}
\end{wrapfigure}

Um die Stellung der Achsen ermitteln zu können ist beim Einschalten eine Referenzfahrt nötig. Die Referenz setzt sich aus mehreren Schaltern zusammen, die physikalisch am Ende jeder Achse positioniert sind und schließen, wenn der Schlitten die Position (0,0,0,0,0) in X,Y,Z,A,B erreicht hat. Weitere Schalter werden nötig, wenn man ermitteln möchte ob der Automat offen oder geschlossen ist. Dafür wurden 10 digitale Eingänge auf dem Board reserviert. Alle Eingänge sind galvanisch über Optokoppler vom Typ IL217AT getrennt. In Abbildung \ref{OptoKop} ist exemplarisch für alle Eingänge dargestellt, wie die galvanische Trennung realisiert wurde. Das Ziel war, einen weiten Bereich von 0 - 24 Volt zu ermöglichen, ohne die LED durch einen zu großen Strom zu zerstören. Der Kondensator wurde hinzugefügt, um einem Prellen der Taster entgegenzuwirken. Durch den Kondensator lässt sich eine Zeitkonstante festsetzen, die der Schalter eingeschaltet sein muss um die Vorwärtsspannung der LED zu überwinden. Der 100k$\Omega$ Widerstand ist aufgrund der kleinen Eingangsimpedanz (etwa 30k$\Omega$) des Mikrocontrollers eigentlich unnötig, wurde aber dennoch als Option eingebaut. Der Zustand der Pins (in diesem Fall DIN0) kann nach der Initialisierung direkt durch 'DIN\_0\_VAL' abgefragt werden. Verantwortlich dafür ist folgendes Makro, welches 0x00 zurückgibt wenn der Pin nicht auf HIGH liegt und eine Zahl verschieden 0x00 wenn der Pin auf HIGH liegt.
\begin{verbatim}
#define DIN_0_VAL (*((volatile uint32_t *)(GPIO_PORTB_BASE + \\

(GPIO_O_DATA + ( 0x20 << 2 )))) >> 5)
\end{verbatim} 
Um Flexibilität zu gewährleisten wurden die Eingänge der Optokoppler über Schraubklemmen nach außen geführt.
 
 \subsection{UART Schnittstelle}
 Der Mikrocontroller bietet zwar eine USB Device Schnittstelle, doch die Einarbeitungszeit in den von TI bereitgestellten USB-Stack oder gar die Programmierung eines eigenen Stacks würde den Umfang einer Projektarbeit weit übersteigen. Da keine großen Mengen an Daten in kurzer Zeit übertragen werden müssen bietet sich hier an, die UART Schnittstelle des Controllers zu nutzen. Der RS232 Standard schreibt allerdings vor, dass eine Verbindung über die serielle Schnittstelle mit Spannungspegeln von -12V und 12V kodiert wird, welche den Eingang des Controllers zerstören würden. Grundsätzlich gibt es zwei Lösungen dafür:
 \begin{itemize}
 \item{Man nutzt einen USB$<>$UART Konverter, der einen TTL kompatiblen Ausgang hat.}
 \item{Man nutzt einen Levelkonverter mit Ladungspumpe um auf die vom RS232 Standard geforderten Spannungen zu kommen.}
 \end{itemize}
Als UART$<>$USB Konverter bietet sich der FT232RL an - Der Chip wurde zum Defakto-Standard in der Hobbyelektronik, da er einerseits günstig und andererseits einfach zu handhaben ist. Der FT232RL wäre für diesen Zweck hardwareseitig gut geeignet. Problematisch wird es allerdings auf der Treiberseite. Der Chip emuliert eine virtuelle COM Schnittstelle. Microsoft Windows hat den Treiber allerdings nicht im Repository oder bereits installiert. Daher muss der Treiber umständlich von der Webseite heruntergeladen werden. Bei neueren Versionen von Windows kann es auch vorkommen, dass der Treiber gar nicht erst funktioniert. 
Daher wurde die Schnittstelle als RS232 Schnittstelle mit einer Sub-D9 Buchse über einen Levelkonverter vom Typ MAX3232(CSE) herausgeführt. Der Levelkonverter ist ebenfalls eine bewährte Methode, eine nach dem RS232 Standard entworfene Schnittstelle bidirektional auf ein anderes Spannungslevel bei Baudraten von bis zu 1MBaud zu bringen.
 
\begin{figure}[h]

\hspace{-14pt}
\caption{Beschaltung des MAX3232 Levelshifters.}
\label{LevelShift}
\end{figure} 
Abbildung \ref{LevelShift} zeigt die Beschaltung des MAX3232 und der Sub-D9 Buchse. Es sind lediglich die TXD und RXD Leitungen herausgeführt - eine Flusssteuerung ist nicht nötig, da der Mikrocontroller seinen Takt von einem 16MHz Quarz ableitet und somit keinen Baudratenfehler hat, mit 9600baud übertragen wird und die Leitungslänge sehr gering ist. CTS, RTC, DTR, etc sind nicht beschaltet, da der Microcontroller keine USART besitzt und eine synchrone Übertragung aufgrund des paketbasierten Kommunikationsprotokolls nicht notwendig ist. \newline
Die Bootstrapkondensatoren C39 bis C42 sind im Datenblatt als Elektrolytkondensatoren angegeben, Bipolarkondensatoren funktionieren allerdings genauso gut und sind in diesem Kapazitätsbereich noch kleiner als Elkos. Elektrolytkondensatoren wären notwendig, wenn es auf den Innenwiderstand (ESR - Equivalent Series Resistance) oder auf große Kapazität ankäme. Beides ist hier nicht der Fall. 

 \subsection{Netzwerkschnittstelle}
Da die Elektronik auch mit dem Intranet und vielleicht sogar mit dem Internet kommunizieren sollte, ist eine Netzwerkschnittstelle nötig gewesen. Da zum Zeitpunkt der Entwicklung der Platine noch nicht die ganze Tiva C Serie sondern nur einige wenige Exemplare ohne integrierte MAC und PHY Peripherie verfügbar waren, wurde der TCP/IP Stack über einen eigenen IC realisiert. Als Controller wurde der W5500 von Wiznet ausgewählt, da der Vorgänger im Hobbybereich als einfach ansteuerbar galt und Wiznet mit dem W5500 an den Erfolg des W5200 anknüpfen wollte. Als Alternative wurde der ENC424J600 in Betracht gezogen. Beide Stacks schneiden bei einem direkten Vergleich etwa gleich gut ab. Ausschlaggebend war die weite Verbreitung, der am Anfang stehende Produktzyklus und die Tatsache, dass es für den Wiznet Chip bereits vorgefertigte Bibliotheken gibt, die lediglich eingebunden werden müssen und somit schnell benutzbar gemacht werden können. \newline
In Abbildung \ref{SchemNetwork} ist die Ansteuerung des Stacks zu sehen. Der Chip benötigt einen 25 MHz Quarz, der relativ nahe am Chip sitzt um einerseits Störeinflüsse vom Quarz und andererseits Störeinflüsse zur Taktversorgung hin zu vermeiden. Ausserdem verkleinert man den Einfluss, den die Kapazitätsbeläge der Leitungen auf den Oszillator haben. Die Widerstände R42 bis R48 sind Pulldown Widerstände für chipinterne Peripherie. Weiterhin sorgen die der Netzwerkbuchse vorgeschalteten Widerstände für eine Begrenzung des Stromflusses durch die Transformatorspulen, die zur galvanischen Trennung vorgesehen sind. \newline
Der Wiznet Chip übernimmt sowohl die Flusskontrolle als auch die physikalische Anbindung an das Netzwerk. Die Pakete, auf denen TCP und UDP basieren, müssen allerdings vom Mikrcontroller erstellt, gelesen und interpretiert werden. Da diese Arbeit nicht den fertigen Automaten, sondern einen Entwicklungsstand beschreibt, wurde der Chip zwar beschaltet, konnte durch fehlende Software allerdings noch nicht getestet werden.

\subsection{Motorcontroller}
\label{Motorcontroller}
Da die Elektronik keine Motorendstufen ansteuern sollte sondern selbst als 'All in One' Lösung dienen sollte, wurden drei Konzepte in Betracht gezogen:
\begin{itemize}
\item{Die Endstufen werden durch diskrete MOSFET Transistoren mit zugehörigen MOSFET Treiberchips realisiert. Zusätzlich zu den FETs muss noch eine Stromüberwachung- und Begrenzung in den Lastkreis eingebaut werden um bei Stillstand der Motoren einen maximalen, einstellbaren, Strom fließen zu lassen, der das Drehmoment der Motoren aufrecht erhält, die Motoren aber nicht durch thermische Überlast zerstört.}
\item{Die Endstufen werden durch integrierte Halb- bzw Vollbrücken mit eingebauter Stromüberwachung realisiert. Dadurch entfällt eine Strommessung und Stromregelung.}
\item{Die Endstufen werden durch vollintegrierte Motortreiber realisiert, die über einen Bus mit der Logik verbunden sind.}
\end{itemize}
Der Vorteil der ersten Lösung liegt in der Möglichkeit, durch eine geeignete Auswahl der MOSFETs eine Endstufe zu realisieren, die eine (in Grenzen) beliebig hohe Stromlieferfähigkeit besitzt und somit mit beliebig großen Motoren belastet werden kann. Der Nachteil liegt im Entwicklungsaufwand, der - insbesondere im Rahmen einer Projektarbeit - in Grenzen gehalten werden sollte. Am Ende soll ein Automat das Ziel der Arbeit sein und nicht, eine Endstufe für Schrittmotoren zu entwickeln. \newline
Der zweite Ansatz löst das Problem durch eine integriere Strommessung und Stromregelung. Damit lässt sich einiges an Zeit und Platinenfläche einsparen. Ein Nachteil dieser Lösung ist die beschränkte Auswahl an modernen integrierten Halb- und Vollbrücken in von Hand lötbaren Gehäusen. Weiterhin muss der Mikrocontroller wie bei Ansatz 1 auch die Beschleunigungsrampen für die Motoren generieren. \newline
Der dritte Ansatz stellt sich somit als die schnellste und einfachste heraus. Der Nachteil ist hier, dass die Auswahl an vollintegrierten Motortreibern mit großer Leistung noch kleiner ist als die Auswahl an Halb/Vollbrücken. \\
\\
Der eingesetzte L6470\footnote{Datenblatt: \url{http://www.st.com/web/en/resource/technical/document/datasheet/CD00255075.pdf} (Vom \today)} von STMicroelectronics passt laut Datenblatt sehr gut auf das Anforderungsprofil, ist im PowerSOT36 Gehäuse verfügbar und lässt sich per SPI an den Mikrocontroller anbinden. Laut dem Datenblatt lässt der Treiber auch den Betrieb in einer SPI Daisychain zu wodurch sich die Anzahl der benutzten Pins am Controller auf vier (SDI,SDO,SCLK,!CS) reduziert. Zudem beinhaltet der Chip einen digitalen Signalprozessor, der nach Einstellung der Parameter sowohl die Rampen ,um Beschleunigen und Abbremsen zu können, generiert, als auch den angeschlossenen Motor überwacht, die Betriebsspannung und den Motorstrom regelt, Stillstand und Schrittverlust erkennt und eine hardwareseitige Abschaltung durch einen seperaten Schaltereingang ermöglicht. Abbildung \ref{SchemMotor} zeigt die Beschaltung der Treiber mit der Ladungspumpe zur Ansteuerung der internen MOSFETs. Alle Motorcontroller können vom Mikrocontroller zurückgesetzt werden. Zusätzlich dazu kann jeder Controller über den !FLAG Pin anzeigen, wenn ein Problem oder Ausnahmezustand vorliegt. Die BUSY Pins sind nicht beschaltet, da jeder Controller den Zustand des Pins in einem Register ablegt und somit auslesbar macht. Der 'SW' Eingang liegt bei allen Controllern an einem über Optokoppler schaltbaren Eingang und stellt einen NOTAUS dar: Sobald der Eingang auf HIGH geht, stoppen die Motortreiber die Motoren mit möglichst hoher Abbremsgeschwindigkeit und schalten die Ausgänge dann auf HIGH-Z wodurch die Motoren stromlos werden.

\subsection{Platinenlayout}
Die Platine ist aufgrund der Packungsdichte vierlagig (Siehe Abbildung \ref{Board}. Beim Layout wurde darauf geachtet, den Digitalteil vom Leistungsteil zu trennen, da über den Widerstand des Kupfers bei hohen Strömen eine Spannung abfällt und Logikpegel verfälschen könnte. Der Spannungsabfall ist umgekehrt proportional zur Dicke und Breite der Leiterbahn. Eine große Massefläche bietet also einen kleineren Widerstand als eine 20mil Leiterbahn. \newline
Die Sektionen sind auf allen vier Layern gleich. Somit ist die Platine dreigeteilt: Der dritte Teil ist die Bank die die digitalen Eingänge beinhaltet. Diese sind durch Optokoppler galvanisch getrennt und benötigen somit eine eigene (wenn auch gemeinsame) Masse. Im digitalen Teil wurde auf den obersten Layer die Spannungserzeugung und - soweit möglich - auch die Spannungsversorgung für die einzelnen Bausteine gelegt. Ausserdem befinden sich auf dem Top Layer noch die Signale für die Schnittstellen (LAN, RS232, DIN, JTAG) und die Taktversorgung. Der Layer darunter beherrbergt die Spannungsversorgung des DCDC Wandlers und die Signale für die Motortreiber.
Die beiden Bottomlayer führen die Betriebsspannung für die digitalen Eingänge, die Spannungen für den Digitalteil der Motortreiber und verstreut einige Signale, die sonst nicht anders geroutet werden konnten. \newline
Die beiden Top Layer im Leistungsteil wurden dazu benutzt, die Signale der Motortreiber zu verteilen, damit die große freie Fläche als Kühlkörper genutzt werden kann. Je nach Belastung ist dennoch ein Kühlkörper nötig. Der erste Bottom Layer (Gezählt wird immer von der Oberseite der Platine) führt die Spannungsversorgung der MOSFETs und die Ausgänge der Treiber zu den jeweiligen Klemmen. Der zweite Bottom Layer dient durch die Vias an den Kanten des Layers als Kühlkörper und thermische Kapazität um Lastspitzen abzufangen.

\subsection{Errata}
\begin{itemize}

\item{Der Clock für die Motortreiber heißt am Mikrocontroller SPI\_CLK und an den Bausteinen SPI\_CLOCK. Das bedeutet, dass der SPI-Takt nicht zu den Motortreibern gelangt. In der aktuellen Revision wurde das mit einem Kabel vom Mikrocontroller zur SPI\_CLOCK Leitung notdürftig behoben}

\item{Das !MOT\_RESET Signal der Motortreiber liegt auf keinem Potential. In der aktuellen Revision wurde das mit einem Kabel vom VCC Bus zur !MOT\_RESET Leitung notdürftig behoben. In der Revision 2 sind die Motortreiber mit PD5 des Mikrocontrollers verbunden.}

\item{Der Spannungsregler (IC1) von 5V auf VCC kann mit Hochschulmitteln im QFN Gehäuse nicht ohne größeren Aufwand platziert und gelötet werden. Ein Ersatz ist ein LT1117 der auf die Platine geklebt und mit Drähtchen verbunden wird}

\item{Die Ansteuerung der Motortreiber mittels Daisychain hat sich als unnötig schwierig herausgestellt. Daher werden in Revision 2 alle Treiber parallel an den Bus angeschlossen und über den Chip Select Eingang ausgewählt oder auf einer eigenen Platine untergebracht.}

\item{Eine gesonderte Spannungsversorgung hat sich als unnötig erwiesen. Die Idee dahinter war, die Motortreiber mit ihrer Maximalspannung zu versorgen damit die Motoren bei hoher Drehzahl ein größtmögliches Drehmoment haben. Da der Schaltregler allerdings schon geroutet war und die Maximalspannung der Motortreiber über dem Limit des Konverters liegt, wurde, um Zeit zu sparen, eine zweite Spannungsversorgung etabliert. In Version 2 wird ein Spannungsregler eingesetzt, dessen Maximalspannung über der der Motortreiber liegt.}

\item{Die RS232 kompatible Schnittstelle nimmt zu viel Platz auf der Platine weg. In Version 2 wird die USB Schnittstelle des ARM genutzt, um eine virtuelle serielle Schnittstellenkommunikation zu ermöglichen.}

\item{Die Lösung zur Ethernetkommunikation in Version 1 ist unbefriedigend, da man von einem relativ kleinen Chiphersteller abhängig ist. Weiterhin benötigt die Lösung mit Ethernetchip zu viel Platz auf der Platine. Leider war die vollständige Microcontrollerfamilie des Herstellers Texas Instruments zur Entwicklungszeit nur unter NDA einzusehen. Zum Zeitpunkt der Erstellung dieses Dokuments werden Microcontroller mit komplettem MAC und PHY Layer in der Tiva Familie gelistet. Version 2 wird die jetzige Lösung ersetzen und den TCP/IP Stack in den Mikrocontroller integrieren.}

\item{Es sollte eine Oufferbatterie für den Microcontroller eingebaut werden um Register vor einem Stromausfall noch speichern zu können. Eventuell genügt auch ein kleiner oder auch ein großer Kondensator, mit dessen Hilfe ein Brownout verhindert werden kann. }

\item{Die Benutzerkommunikation erfordert einen weiteren Mikrocontroller als SPI Slave. Diese Lösung ist unbefriedigend, im Hinblick auf den Zeitaufwand jedoch nicht anders machbar. Version 2 wird hinter ein Display geschraubt werden können, einen Dekoder für Tastatureingaben haben und mehr Pins am Mikrocontroller verfügbar haben. }
\end{itemize} 

%%%%%%%%%%%%%%%%%%%%%%%%%%%%%%%%%%%%%%%%%%%%%%%%%%%%%%%%%%%%%%%%%%%%%%%%%%%%%%%%%%%%%%%%%%%%%%%%%%%%%%%%%%%%%%%%%%%%%%%%%%%%%%%%%%%%%%%%%%%%%%%%%%%%%%%%%%%%%%%%%
\newpage
\section{Software}

In diesem Kapitel wird der Ablauf und die Logik der Software erläutert, sowohl in der tatsächlichen Ausführung, als auch in der Planung für eine spätere, umfangreichere Version.
Das grundliegende Konzept der Software ist eine durch Aufträge gesteuerte Zustandsmaschine. Die Maschine selbst dient lediglich der Dekodierung und Interpretation von Aufträgen, die über eine Schnittstelle übermittelt  und danach in Befehle für die Motortreiber umgesetzt werden.  Die Software selbst weiss nicht, welche Kiste welche Größe und welchen Inhalt hat. Aus diesem Grund muss ein externes Verwaltungsprogramm,  im folgenden als "höhere Logik" bezeichnet, die Verwaltung des Boxeninhalts übernehmen.\\
Im Groben kann man die Software in 5 Aufgabenbereiche einteilen:
\begin{enumerate}
	\item Die State-Machine
	\item Die Schnittstellenkommunikation und Nachrichtendekodierung
	\item Das Verwalten und Abarbeiten der Aufträge
	\item Die Steuerung der Mechanischen Komponenten
	\item Die Fehlererkennung und Behebung
\end{enumerate}
 Wird eine Nachricht über die Schnittstelle empfangen, wird sie in einer Interrupt-Service-Routine in einem Ringpuffer abgespeichert und später inder State-Machine dekodiert, und auf Richtigkeit überprüft. Wenn ein gültiger Auftrag empfangen wurde, wird er in Motorenbefehle umgesetzt.\\
Sollte dabei an einer Stelle ein Fehler erkannt werden, wird dieser im Zustand STATE\_ERROR behoben.

\subsection{Verwendete Programmbibliotheken}
Texas Instrument liefert für den Tiva Microcontroller die Bibliothek Tivaware Peripheral Driver Library mit. Diese enthält Header-Dateien, mit API-Funktionen zur vereinfachten Ansteuerung des Microcontrolers. Diese Bibliothek beinhaltet alle Header-Dateien, die ansonsten nicht explizit erläutert werden.\\
Darüber hinaus bedienen wir uns einer Bibliothek namens \textit{dSpin.obj}. Diese Bibliothek vereinfacht das Ansteuern der einzelnen Motortreiber.\\
Die Bibliothek wurde vom Hersteller der Motortreiber, STMicroelectronics, für Kunden erstellt und bereitgestellt. Alle Funktionen, Variablen und Definitionen in dSpin.c und inc\_dSpin.h sind Teil dieser Bibliothek, die auf \url{www.st.com} kostenlos erhältlich ist. 

\subsection{Die State-Machine}
Die State-Machine stellt die Verbindung zwischen den einzelnen Segmenten dar und verwaltet und steuert deren Aufruf.\\
Realisiert wurde die State-Machine mit einer switch-case Anweisung, dessen Argument ausschließlich in der State-Machine selbst verändert wird. 
\begin{verbatim}
	switch(SYS_STATE){
	case STATE_STARTUP: (...)
	case STATE_ERROR: (...)
	case STATE_JOB_HANDLING: (...)
	case STATE_MSG_HANDLING: (...)
	case STATE_UART_COM: (...)
	case STATE_MOT_COM: (...)
	case STATE_NET_COM: (...)
	case STATE_IDLE: (...)
	}
\end{verbatim}

\subsubsection{STATE\_STARTUP}
Der Zustand STATE\_STARTUP wird beim Systemstart aufgerufen und bereitet alle nötigen Register und Speicherbereiche für den Betrieb vor und fährt anschließend die Motoren zum Koordinatenursprung (Home-Position). Nach der Initialisierung wird der Zustand STATE\_IDLE aufgerufen.

\paragraph{./setup\_INT}
Mit setup\_INT werden die jeweiligen Interruptquellen aktiviert und anschließend die API-Funktion IntMasterEnable aufgerufen, um Interrupts zu ermöglichen.

\paragraph{setup\_GPIO}
Mit setup\_GPIO werden die General-Purpose-Input\textbackslash Output Ports aktiviert. Für den laufenden Bertrieb ist die Aktivierung von Port A relevant, da Die UART Pins auf Port A liegen und auch als solche initialisiert werden müssen. Zusätzlich sind zum Debuggen die  LEDs an den Pins 1 bis 3 von Port F als Output initialisiert. 

\paragraph{setup\_UART}
In setup\_UART wird die UART-Peripherie aktiviert und initialisiert. Als Workaround für ein Problem das bei der Entwicklung aufgetreten ist, liegt der Transmit-Interrrupt auf EOT, also End-of-Transmission. Das bedeutet, dass der Transmit-Interrupt ausgelöst wird, wenn eine Übertragung endet. Siehe auch: Init\_Transmission. 
%wie referenziere ich?% 

\paragraph{setup\_JOB\_QUEUE}
In setup\_JOB\_QUEUE wird die Job-Warteschlange initialisiert. Vorerst wird nur eventueller "Datenmüll" entfernt, also alle Elemente zu Null gesetzt. Allerdings wäre es mit physikalischen Speichermedien möglich, die Warteschlange von diesen abzurufen.

\paragraph{setup\_HOME\_POS}
setup\_HOME\_POS fährt die Motoren an den Koordinatenursprung und legt diesen als Home-Position fest. Derzeit ist setup\_HOME\_POS noch auskommentiert, da die Funktionalität der Motorensteuerung erst getestet werden muss (siehe: Abschnitt Elektronik).
%referenzierung hier einfügen oder beisatz löschen - jans entscheidung%

\subsubsection{STATE\_ERROR}
Der Zustand STATE\_ERROR dient zur Bearbeitung und Behebung erkannter Fehler. Nach der Bearbeitung eines Fehlers wird außerdem eine Nachricht an die höhere Logik gesendet.
\\
Beim Auftreten eines Fehlers wird jeweils ein entsprechendes Fehlerflag gesetzt, welche im STATE\_ERROR der Reihe nach abgefragt werden. Diese Fehlerflags sind definiert als:
\begin{verbatim}
typedef struct sError {
	uint32_t	SER;
	uint32_t	STA;
	uint32_t	ETH;
	uint32_t	MSG;
	uint32_t	MOT;
	uint32_t	JOB;
} sErrorFlags;
sErrorFlags eState;
\end{verbatim}
Bei der Fehlerbearbeitung wird der Wert des jeweils zur Fehlerquelle zugehörigen Elements abgefragt und mit definierten Werten abgeglichen. Gesetzt werden die Flags, indem sie mit einem entsprechenden Wert ODER-verknüpft werden, bzw mit EXOR, um sie zu löschen.\\
Nach der Behandlung der Fehler wird der Zustand STATE\_UART\_COM aufgerufen und die höhere Logik wird von der Art des Fehlers unterrichtet.

\subsubsection{STATE\_JOB\_HANDLING}
Der Zustand STATE\_JOB\_HANDLING übernimmt die zuvor dekodierte Nachricht und fügt sie zur Job Warteschlange hinzu, schreibt eine Bestätigung für die höhere Logik in den Sende-Ringpuffer und ruft den Zustand STATE\_UART\_COM auf.

\subsubsection{STATE\_MSG\_HANDLING}
Der Zustand STATE\_MSG\_HANDLING entnimmt die empfangene Zeichenkette aus dem Zeichenpuffer und dekodiert sie. Anschliessend wird die Nachricht auf Inhalt und Echtheit überprüft und in einen Puffer geschrieben. Dann wird der Zustand STATE\_JOB\_HANDLING aufgerufen.

\subsubsection{STATE\_UART\_COM}
In STATE\_UART\_COM werden zwei Funktionen ausgeführt: Zum einen wird eine empfangene Nachricht aus demEmpfangs-Ringpuffer in einen Zeichenpuffer geschrieben und auf dessen Überlauf geprüft, zum anderen wird überprüft, ob eine Sendeanfrage aussteht, woraufhin der Sendevorgang initialisiert wird.

\paragraph{Init\_Transmission}
Aufgrund von Problemen beim Einrichten der UART-Kommunikation ist aus Zeitgründen dieser Workaround entstanden: Init\_Transmission fügt "'manuell"' das erste Zeichen des Ringpuffers in den FIFO. Nachdem das erste Zeichen übertragen wurde, wird der EOT-Interrupt ausgelöst und die Übertragung läuft in der ISR automatisch (wie ursprünglich geplant) weiter.

\subsubsection{STATE\_MOT\_COM}
STATE\_MOT\_COM ist ausschliesslich für die Steuerung der Motoren zuständig. Beim Aufruf von STATE\_MOT\_COM wird der aktuell zu bearbeitende Job anhand des OpCodes abgehandelt. Nach Bearbeitung des Jobs wird der Job gelöscht und STATE\_UART\_COM wird aufgerufen, um der höheren Logik die erfolgreiche Bearbeitung des Jobs mitzuteilen.

\subsubsection{STATE\_NET\_COM}
Dieser Zustand ist für eine eventuelle spätere Anbindung an ein Netzwerk vorgesehen, wird derzeit aber noch nicht genutzt.

\subsubsection{STATE\_IDLE}
In STATE\_IDLE wird ein Job aus der Warteschlange in den aktuell zu bearbeitenden Job geschrieben, falls dieser leer ist. Anschließend wird STATE\_MOT\_COM aufgerufen. \\
Wenn die Job Warteschlange leer ist wird 'IDLE' an die höhere Logik geschickt.

\subsection{Die Schnittstellenkommunikation}
Um die Befehle der höheren Logik umsetzen zu können, muss der Automat sie erst einmal bekommen: diese Aufgabe übernimmt eine serielle Schnittstelle.\\
In der Interrupt-Service-Routine werden 3 Aufgabenbereiche bearbeitet:
\begin{itemize}
\item Empfangsinterrupts:\\
Wird eine Nachricht empfangen, so wird entweder UART\_INT\_RX oder UART\_INT\_RT ausgelöst. RX wird ausgelöst wenn der FIFO voll ist und RT wenn ein Line-Timeout entdeckt wird. Line-Timeout bedeutet, dass für einen längeren Zeitraum nichts mehr empfangen wurde.

\item Sendeinterrups:\\
Wenn Daten erfolgreich gesendet wurden, wird UART\_INT\_TX ausgelöst. Dies geschieht so oft, bis die komplette Nahricht übertragen wurde. Für den Fall dass der Interrupt noch nicht ausgelöst wurde, aber eine Sendeanfrage aussteht wird zusätzlich noch auf SER\_TX\_REQUEST abgefragt.

\item Fehlerinterrupts:\\
Wenn bei der Übertragung ein Fehler auftritt, wird einer der folgenden Interrupts ausgelöst:\\
UART\_INT\_OE, UART\_INT\_BE, UART\_INT\_PE, UART\_INT\_FE. Diese stehen, der Reihenfolge nach, für Overrun Error, Break Error, Parity Error und Framing Error.

\end{itemize}
Zu Beginn der ISR wird das Interrupt-Status Register ausgelesen, zwischengespeichert und danach zurückgesetzt, damit die ISR nicht mehrfach aufgerufen wird. Anhand des ausgelesenen Status Registers wird bestimmt, welche der drei Aktionen ausgeführt werden - es sind mehrere möglich, da sie der Reihe nach abgefragt werden.

\subsubsection{Empfangen}
Wenn eine Nachricht empfangen wurde, werden die Zeichen aus dem FIFO in den Ringpuffer geschrieben und auf '\textbackslash n' abgefragt. Hierbei wird außerdem auch der Ringpuffer auf Überlauf überprüft. Wurde ein '\textbackslash n' empfangen, so ist die Nachricht komplett und der Zustand STATE\_UART\_COM wird aufgerufen, sowie das Flag eState.SER mit dem definierten Wert SER\_RX\_MESSAGE\_COMPLETE ODER-verknüpft und die Interruptquelle wird aus dem Status-Puffer gelöscht.

\subsubsection{Senden}
Wenn eine Nachricht gesendet werden soll, wird der Inhalt des Ringpuffers Stück für Stück in den FIFO geschrieben. Anschließend wird die Interruptquelle aus dem Status-Puffer gelöscht, und aus dem Flag eState.SER wird der Wert SER\_TX\_REQUEST mit EXOR gelöscht.

\subsubsection{Fehler}
Wird einer der Error-Interrupts ausgelöst, so wird dieser hier ausgewertet und ein entsprechendes Flag gesetzt und der Zustand STATE\_ERROR wird aufgerufen.

\subsection{Die Ringpuffer}
Da der FIFO der seriellen Schnittstelle nur 16 Byte groß ist, müssen die Daten, die empfangen oder gesendet werden sollen, zwischengespeichert werden, bis die gesamte Nachricht übertragen wurde.\\
Dafür verwenden wir zwei Ringpuffer: einen für empfangene Nachrichten und einen für Nachrichten, die noch gesendet werden. Diese stehen in circular.obj.\\
Die Ringpuffer sind global angelegt, da sie sowohl in der main-Funktion als auch in der ISR verwendet werden, aber keine Übergabewerte zur ISR möglich sind.

In Inc\_Circular.h sind die Ringpuffer definiert als

\begin{verbatim}
typedef struct Buf {
	uint8_t buf[BUF_SIZE];
	uint32_t rdptr;
	uint32_t wrptr;
	uint32_t size;
} Circ_Buf;
\end{verbatim}

Für die Verwaltung der Ringpuffer sind die im Folgenden erklärten Funktionen zuständig.

\subsubsection{getChar}
Die Funktion getChar liest ein Zeichen aus dem Ringpuffer aus, erhöht den Lesezeiger (rdptr) und gibt das Zeichen zurück. Überschreitet der Lesezeiger die Arraygröße von buf[BUF\_SIZE] wird er auf 0 gesetzt. Wenn der Ringpuffer leer ist, gibt die Funktion EXIT\_BUFFER\_EMPTY zurück.

\subsubsection{putChar}
Die Funktion putChar schreibt ein Zeichen in den Ringpuffer, erhöht den Schreibzeiger (wrptr) und gibt EXIT\_SUCCESS zurück.
Überschreitet der Schreibzeiger die Arraygröße von buf[BUF\_SIZE] wird er auf 0 gesetzt. Wenn der Ringpuffer voll ist gibt die Funktion EXIT\_BUFFER\_FULL zurück.

\subsubsection{getRemBufSpace}
Die Funktion getRemBufSpace vergleicht die relative Position von Schreib- und Lesezeiger des übergebenen Ringpuffers miteinander und ermittelt daraus den verfügbaren Speicherplatz und gibt diesen zurück.

\subsubsection{putMsg}
Die Funktion puMsg verwaltet das Einfügen einer Nachricht in den Ringpuffer. Bei Erfolg gibt die Funktion EXIT\_SUCCESS zurück, bzw. EXIT\_FAILURE wenn nicht genug Speicherplatz verfügbar ist. \\
Zur Überprüfung des Speicherplatz wird die Funktion getRemBufSpace aufgerufen und anschließend wird der verfügbare Platz mit dem benötigten verglichen. Bei Erfolg wird die Nachricht Zeichen für Zeichen mit putChar in den Ringpuffer geschrieben.

\subsubsection{getMsg}
Die Funktion getMsg verwaltet das Auslesen einer Nachricht aus dem Ringpuffer. Bei Erfolg gibt die Funktion EXIT\_SUCCESS zurück.\\
Die einzelnen Zeichen werden mit getChar ausgelesen und auf EXIT\_BUFFER\_ EMPTY abgefragt. Ist der Puffer leer, wird EXIT\_BUFFER\_EMPTY zurückgegeben. Bei erfolgreichem auslesen werden die Zeichen in einen Übergabepuffer geschrieben. Wird dieser überschritten, wird EXIT\_BUFFER\_ SIZE zurückgegeben.\\
Wurden alle Zeichen erfolgreich ausgelesen und abgespeichert, wird am Ende der Nachricht ein '\textbackslash n' und ein '\textbackslash 0' angehängt, um die spätere Dekodierung zu erleichtern.

\subsubsection{insertString}
Die Funktion insertString fügt eine Zeichenkette ans Ende einer andere Zeichenkette ein. Zuerst wird die länge der einzufügenden Zeichenkette überprüft, um einen Überschreiten des Speicherbereichs zu vermeiden. Danach wird die Zeichenkette elementweise an die andere angehängt.

\subsubsection{clearString}
Die Funktion clearString löscht eine übergebene Zeichenkette Elementweise.

\subsection{Das Job-System}
Jede empfangene Nachricht wird dekodiert und in einen Job gespeichert. Dieser Job enthält alle Informationen, die der Microcontroller benötigt, um die gewünschte Aktion auszuführen. Das Job-System ist so angelegt, dass mit nur geringem Aufwand weitere Funktionen implementiert werden können.\\
Ein Job ist aufgebaut wie Folgt:
\begin{verbatim}
typedef struct Job {
	uint32_t id;
	uint32_t opCode;
	uint32_t coordX;
	uint32_t coordY;
	uint32_t coordZ;
	uint32_t JOINT;
	uint32_t GRIPPER;
	uint32_t opt1;
	uint32_t opt2;
	uint32_t opt3;
	uint32_t crc;
} sJob;
\end{verbatim}
Die Jobs werden in einer Warteschlange und in zwei Puffern gespeichert:  JobBuffer und CurrentJob. JobBuffer ist ein Puffer für die Übergabe des empfangenen Jobs von decodeMsg an addJob, und CurrentJob enthält den aktuell zu bearbeitenden Job. Nach der Bearbeitung eines Jobs wird eine Nachricht an die höhere Logik gesendet. Sollte an irgendeiner Stelle ein Fehler auftreten bzw. entdeckt werden, so wird der fehlerhafte Job gelöscht und die Art des Fehlers, sowie die Job-ID, an die höhere Logik gesendet.\\
Einen Job kann man in vier Teile zusammenfassen: 
\begin{itemize}
\item Die ID ist eine eindeutige Identifikationsnummer, die jedem Job von der höheren Logik zugewiesen wird.
\item Der OpCode gibt die Funktion an, die der Automat durchführen soll. Derzeit vorgesehen sind:
\begin{itemize}
\item manuelle Steuerung durch den Benutzer
\item Warenausgabe
\item Waren auffüllen
\item Rekalibrierung durch den Benutzer
\end{itemize}
\item Die Parameter sind je nach OpCode unterschiedlich zu interpretieren.
\item Die CRC-Kennung ist wichtig um Übertragungsfehler zu erkennen.
\end{itemize}

\subsubsection{decodeMsg}
Die Funktion decodeMsg übernimmt die in getMsg erhaltene Zeichenkette und trennt sie, als ASCII-Zeichen interpretiert, in einzelne Bestandteile auf:
\begin{verbatim}ID[ OPCode, X-Koordinate, Y-Koordinate, Z-Koordinate , Drehgelenk, Greiferstellung, 
Optional1, Optional 2, Optional3 ]CRC-Kennung\end{verbatim}

Das erste Element ist immer die Job-ID, darauf folgen, in eckigen Klammern, der OpCode und die Parameter, welche durch Kommata getrennt sind. Zusätzlich zu den Fahrparametern (X-, Y-, Z- und Greiferkoordinaten) sind zusätzlich auch drei optionale Parameter vorgesehen für eventuelle zukünftige Funktionen. Zum Schluss folgt eine CRC-Kennung.\\
Die Elemente werden durch die Erkennung der trennenden Zeichen aufgeteilt und zwischengespeichert.\\

Nachdem die Elemente getrennt wurden, werden sie der Reihe nach mit atoi() in Zahlenwerte umgewandelt und überprüft:\\
Zuerst wird die ID überprüft, danach die CRC-Kennung und anschließend die Parameter. Bei erfolgreichen Testergebnissen  gibt die Funktion EXIT\_SUCCESS zurück. Wenn einer der Tests einen Fehler findet, gibt die Funktion einen entsprechenden Fehlerwert zurück. 

\subsubsection{validateID}
Die Funktion validateID durchläuft die Job-Warteschlange und vergleicht die darin gespeicherten Job-IDs mit der empfangenen Job-ID. Dies geschieht, um zu verhindern, dass derselbe Job mehrfach ausgeführt wird. Für spätere Versionen des Automats wäre hier auch eine Sicherung gegen Missbrauch möglich, indem man alle empfangenen Job-IDs langfristig speichert und diese ebenfalls zum Vergleich verwendet. \\
Ebenso wäre die Überprüfung nach einem speziellen Code in der ID möglich, als eine weitere Absicherung gegen Missbrauch.

\subsubsection{checkCRC}
Eine zyklische Redundanzprüfung ist zwar vorgesehen, aber noch nicht implementiert. Die Funktion checkCRC ist leer und gibt lediglich ein EXIT\_SUCCESS zurück.

\subsubsection{validateMsg}
Die Funktion validateMsg überprüft die empfangenen Parameter auf deren Inhalt, um eventuelle Schäden am Automaten zu vermeiden. \\
Die Funktionen testet, je nach OPCode, ob bestimmte Sicherheitskriterien eingehalten werden, damit z.B. nicht der Motor an die Wand fährt oder Ähnliches. Bei Erfolg gibt die Funktion EXIT\_SUCCESS zurück, sonst EXIT\_FAILURE.

\subsubsection{addJob}
Die Funktion addJob fügt den empfangenen und überprüften Job zur Warteschlange hinzu. Dazu durchläuft die Funktion die Warteschlange bis zum ersten leeren Element, schreibt dort den Job rein und gibt EXIT\_SUCCESS zurück. Wird kein leeres Element gefunden, gibt die Funktion EXIT\_FAILURE zurück.

\subsubsection{callJob}
Die Funktion callJob entnimmt der Warteschlange einen Job, schreibt diesen in CurrentJob und rückt die Warteschlange auf:\\
Zuerst wird überprüft, ob CurrentJob leer ist oder nicht. Steht noch ein Job in CurrentJob, gibt die Funktion JOB\_PENDING zurück, damit dieser zuerst ausgeführt wird. Ist CurrentJob leer, wird das erste Element der Warteschlange auf Inhalt überprüft. Bei Erfolg wird dieses in CurrentJob geschrieben, bei Fehlschlag gibt die Funktion EXIT\_FAILURE zurück. Nachdem das erste Element in CurrentJob übertragen wurde, werden alle anderen Elemente der Warteschlange eine Position vorgerückt und die dadurch frei gewordenen Elemente der Warteschlange werden gelöscht.\\
Bei Erfolg gibt die Funktion EXIT\_SUCCESS zurück.

\subsubsection{jobDone}
Nach der Bearbeitung, unabhängig von Erfolg oder Misserfolg, werden die jeweiligen Jobs mit jobDone gelöscht. In jobDone wird jedes Element des übergebenen Jobs zu Null gesetzt.

\subsection{Die Motorsteuerung}
Zur Vereinfachung der Motorensteuerung verwenden wir eine Kette von Motortreibern. Da die Motortreiber in Serie geschaltet sind, müsste man aufwendig bestimmen, welchen Motor man ansteuern möchte und den Befehl dann durch die Treiberkette schieben. Um dies zu vereinfachen, bedienen wir uns einer Bibliothek namens \textit{dSpin.obj}. Diese Bibliothek vereinfacht das Ansteuern der einzelnen Motortreiber.\\
Aus Gründen, die bereits in der Einleitung erläutert sind, wurden weder die Motorsteuerbefehle noch die Funktionen in dspin.c (von uns) praktisch getestet. Darum geben sie, zum Debuggen des restlichen Codes, derzeit nur EXIT\_SUCCESS zurück bevor die Befehle ausgeführt werden. Des weiteren sind die Motorsteuerungs-Funktionen in ihrer aktuellen Form lediglich als Testfunktionen gedacht und werden für den fertigen Automaten noch stark verändert werden.

\subsubsection{Remote\_Ctrl\_Motor}
Die Funktion Remote\_Ctrl\_Motor wird im Fernsteuerungsmodus aufgerufen. Der Fernsteuerungsmodus ermöglicht es derzeit allerdings nur, zum Schutz des Automaten, Positionen anzufahren, nicht jedoch freies Fahren. Zuerst wird die Zielposition mit der aktuellen Position verglichen, um die Fahrtrichtung zu ermitteln. Dies geschieht sowohl für die X- als auch für die Y- Koordinate. Anschließend wird gewartet bis die Motoren wieder still stehen, um die gewünschte Greiferstellung einzunehmen. Auch hier wird wieder gewartet bis die Motoren still stehen, und erst danach wird die Z-Poition angefahren. Erst wenn die Motoren wieder still stehen verlässt der Microcontroller die Funktion.

\subsubsection{Ctrl\_Motor}
Die Funktion Ctrl\_Motor ist für die automatische Steuerung des Automaten zuständig. Zu Beginn der Funktion wird ermittelt, ob und welches Sortierfeld verwendet werden soll, anhand der Greiferbreite und Z-Koordinate des auszuführenden Jobs. Anschließend wird ermittelt ob die Ziel-Box geleert oder gefüllt werden soll.\\
Beide Vorgänge benutzen die gleichen Funktionen in der gleichen Reihenfolge, mit der Ausnahme dass für die Ausgabe EmptyBox verwendet wird und beim Nachfüllen RefillBox.\\
Wenn die Box nicht in der ersten Reihe liegt, werden alle Boxen, die davor liegen, mit getBox und putBox in den jeweiligen Sortierschacht gebracht. Anschließend wird mit getBox die gewünschte Box entnommen und entweder mit EmptyBox oder RefillBox zum Ausgabeschacht gefahren, wo die jeweilige Aktion ausgeführt wird. Danach wird die Box mit PutBox zurückgefahren und die umgestellten Boxn werden wieder zurücksortiert, mit getBox und putBox.

\subsubsection{getBox}
Die Funktion getBox fährt eine Position an und holt eine oder mehrere Box(n) aus einem Schacht. \\
Zuerst wird die Fahrtrichtung in X- und Y-Richtung ermittelt und anschliessend die X-und Y-Positionen angefahren. Wenn die Motoren wieder still stehen wird die Greiferstellung angepasst. Hat der Greifer die gewünschte Stellung eingenommen, wird die Z-Position angefahren, der Greifer geschlossen, und damit die gewünschten Boxn gegriffen. Anschließend fährt der Greifer auf die Position Z=0 zurück. Wenn die Motoren wieder still stehen, wird die Funktion verlassen.

\subsubsection{putBox}
Die Funktion putBox fährt eine Position an und stellt eine Box dort ab.\\
Zuerst werden die X- und Y-Positionen angefahren, dann wird die Z-Position angefahren, der Greifer öffnet sich und die Position Z=0 wird angefahren.\\
Wie bei getBox wird zwischen jedem Schritt gewartet bis die Motoren still stehen.

\subsubsection{EmptyBox}
Die Funktion EmptyBox fährt den Ausgabeschacht an und leert dort eine Box aus.\\
Zuerst werden die X- und Y-Positionen angefahren, danach die Z-Position. Im Ausgabeschacht wird der Greifer um $180^{\circ}$ gedreht, um die Box zu leeren. Danach wird der Greifer wieder zurückgedreht, und die Position Z=0 wird angefahren.\\
Wie bei getBox wird zwischen jedem Schritt gewartet bis die Motoren still stehen.

\subsubsection{RefillBox}
Die Funktion RefillBox fährt den Ausgabeschacht an und wartet dort bis vom Benutzer ein Zeichen kommt, dass die Box befüllt wurde.\\
Der Ablauf von RefillBox ist fast identisch mit dem von EmptyBox, nur dass statt der Rotation, um die Box zu leeren, auf einen Tastendruck vom Benutzer gewartet wird - zur Bestätigung dass die Box befüllt wurde.

\appendix

\input{Matthias_appendix}
\input{Jan_appendix}
\input{Gregor_appendix}

\end{document}

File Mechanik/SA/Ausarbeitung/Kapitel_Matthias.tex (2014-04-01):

\input{../Projektarbeit_Bauteileautomat_WIP_begin}

\definecolor{hellblau}{rgb}{0.8,0.8,1}
\definecolor {hellgrün}{rgb}{0.5,1,0.8}
%\usepackage{wrapfig}

\section{Mechanik}

Dieses Kapitel dokumentiert die mechanische Funktionsweise und die Berechnung der zugehörigen Komponenten. Der Automat soll ca. 1000 Boxen enthalten, um eine große Auswahl zu gewährleisten. Damit dies in einer kompakten Bauweise möglich ist, werden drei unterschiedlich große Boxen verwendet. Die Boxen befinden sich in verschiedenen Schächten. 
Ein Schacht besteht aus jeweils zwei L-Profilen, die mit Schrauben an den Aluminiumprofilen der Rückwand befestigt werden. Die Größe der Schächte ist jederzeit änderbar und somit für jede Boxengröße variabel einstellbar. Ein Greifer, der auf X-Y-Z-Achsen verschiebar ist, fährt den ausgewählten Schacht an und greift anschließend die entsprechende Box. An der Seite des Automaten ist ein Rutsche angebracht, die zur Ausgabe der Teile dient. Der Greifer fährt diese an und kann durch ein Drehgelenk die Box um $180^\circ$ drehen und das gewünschte Teil auswerfen.

\subsection{Greifer}

\subsubsection{Anforderungen}

Der Greifer hat den sicheren Transport der Boxen zwischen den Schächten und der Rutsche zu gewährleisten. Er muss ein Drehgelenk beinhalten, das sich um $180^\circ$ drehen lässt. Weiter sind vom Greifer zwei verschieden große Boxen mit einem maximalen Gewicht von 1000g zu befördern. Damit die Ausgabe der Teile nicht zu lange dauert, muss die Geschwindigkeit des Greifvorgangs entsprechend hoch sein.

\subsubsection{Realisierung des Greifers}

Der Greifmechanismus erfolgt über zwei 20cm lange Greifarme aus Aluminium, wobei ein Greifarm fest verbaut ist und der andere über eine Trapezgewindespindel verfahrbar ist. Für den Antrieb der Spindel werden zwei Zahnräder verwendet, welche mit einem Schrittmotor verbunden sind. Damit der bewegliche Greifarm nicht verkantet, wird er über eine zusätzliche Welle geführt. Moosgummi auf dem Greifarm erhöht die Haftkraft zwischen den Boxen und den Greifarmen. Der Drehmechanismus erfolgt ebenfalls über zwei Zahnräder und einen Schrittmotor. Ein Zahnrad ist auf einer Welle befestigt, die auf einer Seite fest mit dem Greifer verbunden ist und auf der anderen Seite in einem Rillenkugellager gelagert ist. Durch das zweite Zahnrad, das durch einen Schrittmotor angetrieben ist, kann die Welle  mit dem Greifer rotiert werden. 

\subsubsection{Antrieb}

Alle relevanten Eigenschaften(Presskraft, Verfahrensgeschwindigkeit und Schrittlänge) sind abhängig vom Schrittmotor 
des Greifmechanismus. Für die richtige Dimensionierung des Schrittmotors sind entsprechende Berechnungen erforderlich.

\begin{itemize}

\item Haltekraft des Greifarms

Das Drehmoment des Motors muss den sicheren Transport einer Box mit einem Gewicht von 1000g gewährleisten. Zur Berechnung des Drehmoments wird die Presskraft benötigt, die der dynamische Greifarm auf die Box ausübt. Hier handelt es sich um einen Erfahrungswert, da verschiedene Berechnungsvariablen (z.b. Reibunkskoeffizent von Polystrol und Moosgummi) nicht vorhanden sind. Der Wert wurde daher auf $F=50N$ ausgelegt und bewußt höher gewählt, damit die Boxen auch bei kleinen Stößen und Vibrationen nicht aus dem Greifarmen rutschen können.\\
\newline

Durch die Umwandlung von einer Drehbewegung in eine Längsbewegung entsteht ein Wirkungsgrad, welcher durch den 
Steigungswinkel des Trapezgewindes und den Gewindereibungswinkel berechnet werden kann.\\

Den Steigungswinkel erhält man durch:

\[tan(\alpha)=\dfrac{P}{d\cdot \pi}=\dfrac{20mm}{4mm\cdot \pi}=\dfrac{5}{\pi}\]

\begin{tabbing}
mit \= P: Spindelsteigung\\
    \> d: Spindelnenndurchmesser  \\
		\> $\alpha$: Steigungswinkel\\
\end{tabbing}

Für ISO-Trapezgewinde mit geschmierter Mutter und einem Reibwert von $\mu=0.04$ erhält man den Gewindereibungswinkel mit:

\[ \rho=\mu\cdot 1.07= 0.04\cdot 1.07=0.043 \]

\begin{tabbing}
mit \= $\rho$: Gewindereibungswinkel\\
    \> $\mu$: Reibwert  \\
\end{tabbing}

Mit dem Steigungswinkel und dem Gewindereibungswinkel kann nun der Wirkungsgrad berechnet werden:

\[\eta=\dfrac{tan(\alpha)}{tan(\alpha +\rho)}=\dfrac{tan(\dfrac{5}{\pi})}{tan(\dfrac{5}{\pi}+0.043)}=3.08\]

\begin{tabbing}
mit \= $\eta$: Wirkunsgrad \\
\end{tabbing}

Das Antriebsdrehmoment der Spindel ergibt sich aus der Presskraft, der Steigung und dem Wirkungsgrad des Trapezgewindes: \\

\[M=\frac{F\cdot P}{1000\cdot 2\pi \cdot \eta}=\frac{50N\cdot 4mm}{1000\cdot 2\pi \cdot 3.08}=0.01Nm\]
\newline

\begin{tabbing}
mit \= M: Antriebsmoment\\
    \> F: Presskraft \\
\end{tabbing}

Auf das Ergebnis müssen die Verluste durch die Lagerung und der Wirkungsgrad der Übersetzung aufgeschlagen werden. Zur Berücksichtigung  dieser Verluste sollte die ausgewählte Leistung des Antriebs um 60\% bis 100\% über dem errechneten Wert liegen.\\

Mit dem Übersetzungsverhältnis der Zahnräder und den Verlusten des Greifmechanismus erhält man das geforderte Drehmoment des Motors durch:

Übersetzungsverhältnis der Zähnrräder:\\
\[i=\frac{z_2}{z_1}=\frac{30}{60}=0.5\]	

das Antriebsmoment des Schrittmotors:\\		
		
\[M_{Motor}=M_{Spindel}\cdot i \cdot R=0.01Nm \cdot 0.5 \cdot 1.6= 8Nmm \]

\begin{tabbing}
mit \= i: Übersetzungsverhältnis\\
    \> R: Reibungsverluste \\
\end{tabbing}

\item Schrittlänge

Die Schrittlänge ist der kleinstmögliche Weg, den der Greifarm zurücklegen kann. Bei einem Schritt des Motors wird dieser Weg zurückgelegt. Alle anderen Wege ergeben sich als ein vielfaches der Schrittlänge. Das weiche Moosgummi auf den Greifarmen und die Elastizität der Boxen erfordern eine feine Abstimmung der Presskraft der Greifarme. Für eine anwendungsgerechte Einstellung ist eine kleine Schrittlänge erforderlich.
\newpage

Mit dem Übersetzungsverhältnis kann die Schrittlänge des Greifers berechnet werden:
\[S=\frac{P}{\frac{360^\circ}{\alpha}}\cdot i=\frac{4mm}{\frac{360^\circ}{1.8^\circ}}\cdot 0.5=0.01mm\]

\begin{tabbing}
mit \= $\alpha$: Schrittwinkel des Elektromotors\\
    \> P: Steigung der Trapezgewindespindel
\end{tabbing}

Die geringe Schrittlänge ist ausreichend um die benötigte Presskraft einzustellen. Toleranzen des Gewindes oder der Schritte des Schrittmotors können vernachlässigt werden.
\newline

\item Geschwindigkeit des Greifarms\\
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

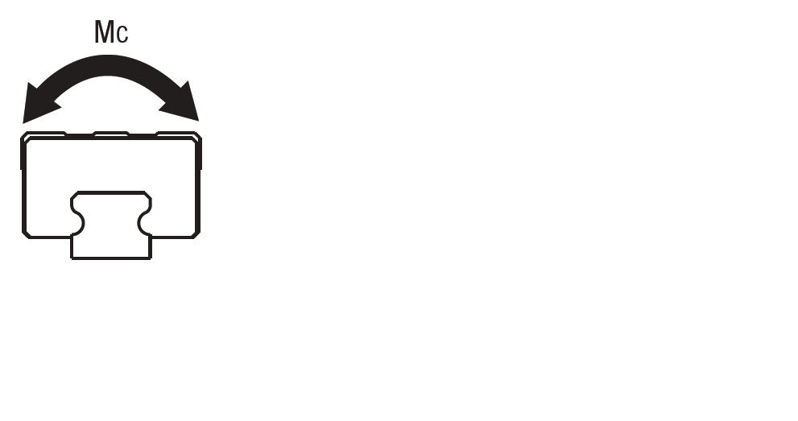
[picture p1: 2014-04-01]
Mechanik/SA/Ausarbeitung/Bilder/Drehmomen_Rollrichtung.png

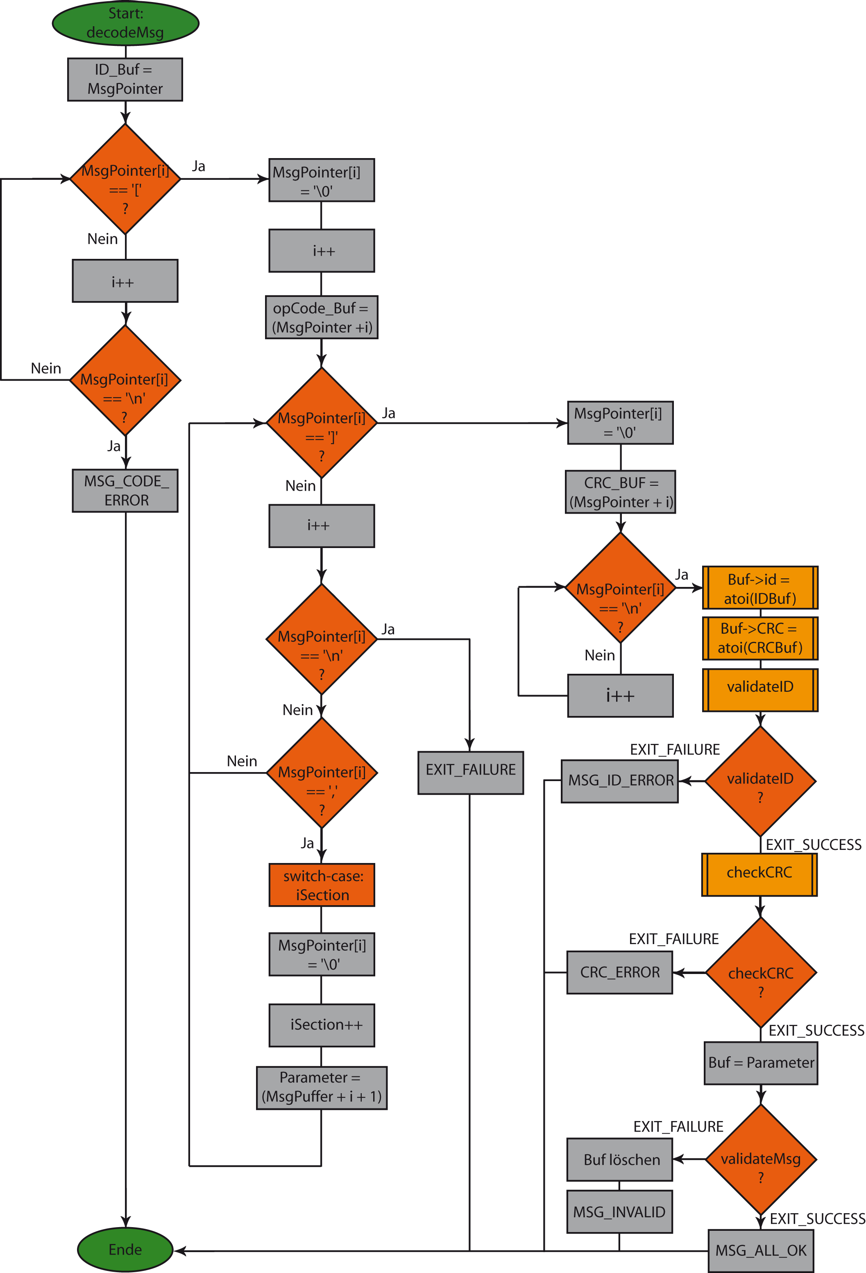
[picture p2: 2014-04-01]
Ausarbeitung/decodeMsg.png

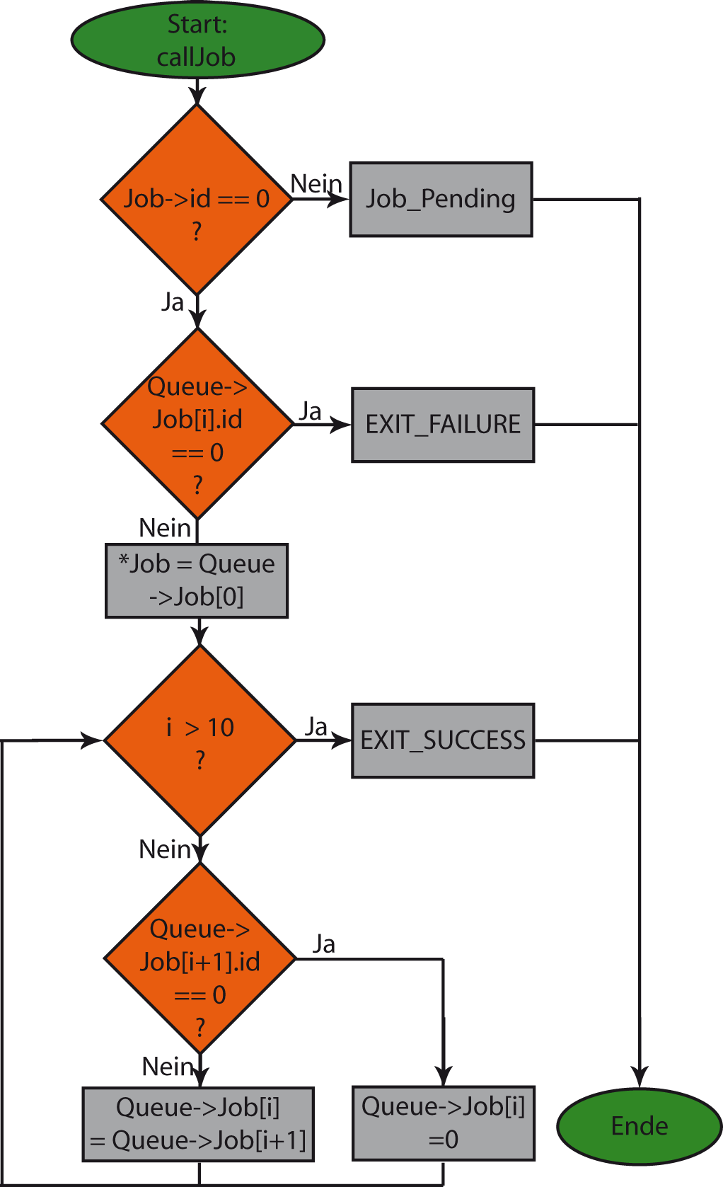
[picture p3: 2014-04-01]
Ausarbeitung/callJob.png

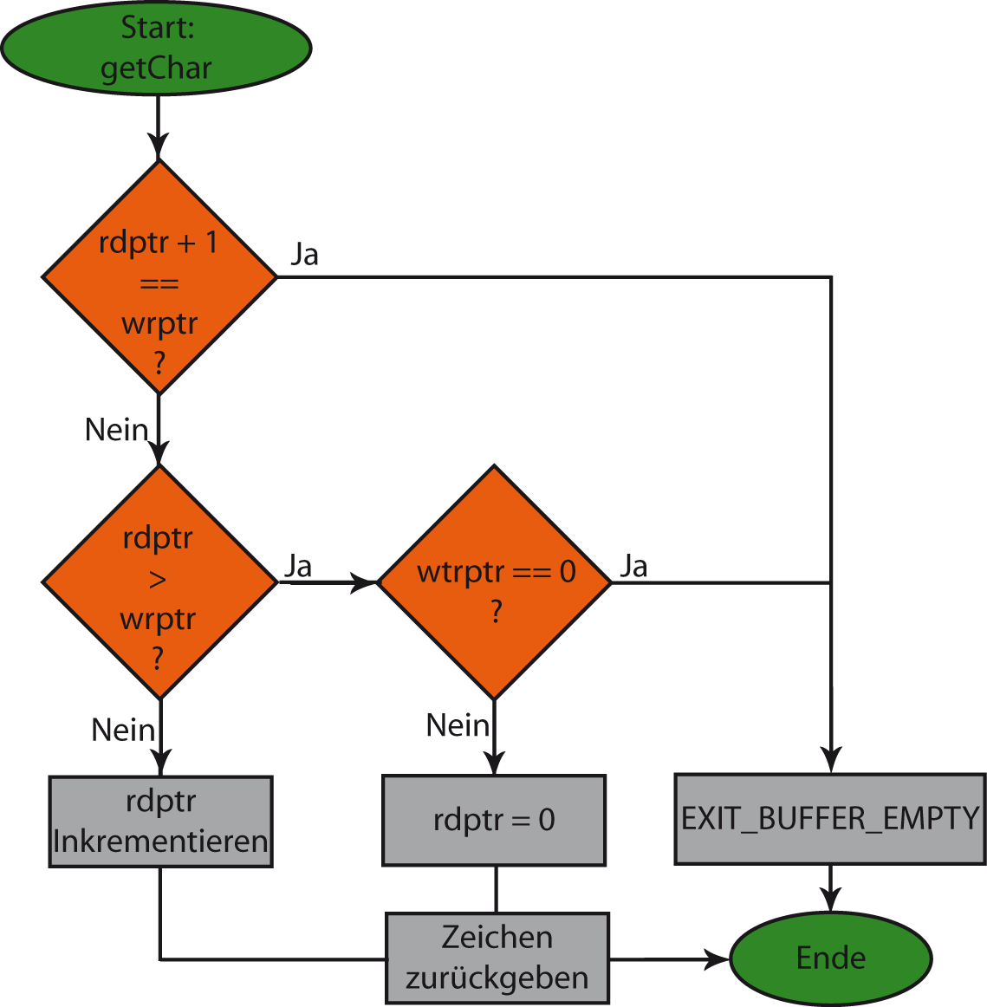
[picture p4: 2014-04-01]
Ausarbeitung/getChar.png

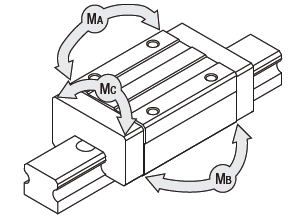
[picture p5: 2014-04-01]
Mechanik/SA/Ausarbeitung/Bilder/Momente.png

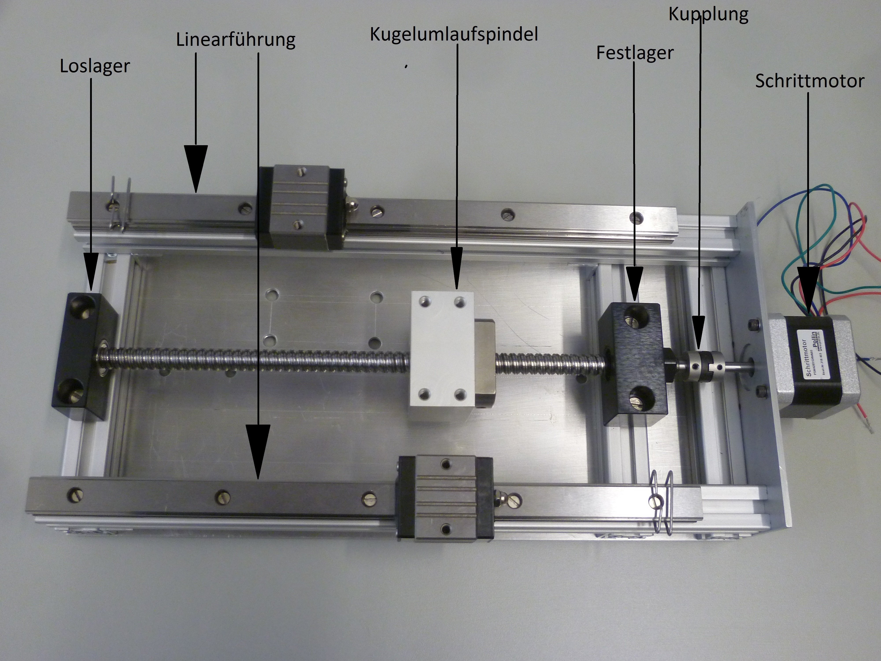
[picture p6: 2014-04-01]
Mechanik/SA/Ausarbeitung/Bilder/Z_Achse.JPG

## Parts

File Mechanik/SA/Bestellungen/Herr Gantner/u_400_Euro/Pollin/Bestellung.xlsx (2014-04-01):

Bezeichnung | Stück | Artikelnummer | Preis/Stück | Preis | Zusatz | URL
Schrittmotor PSM42BYGHW603, 42mm, (http://www.pollin.de/shop/dt/NjQ1OTg2OTk-/Motoren/Schrittmotoren/Schrittmotor_PSM42BYGHW603_1_8_.html) | 3 | 94-310 453 | 15.95 | 47.85 | Bestellung muss per Mail oder Fax gesendet werden, da sonst keine Zahlung per Rechnung möglich ist. | http://www.pollin.de/shop/dt/NjQ1OTg2OTk-/Motoren/Schrittmotoren/Schrittmotor_PSM42BYGHW603_1_8_.html
 |  |  |  | 0
 |  |  |  | 0
 |  |  |  | 0
 |  |  |  | 0
Verandkosten | 1 |  | 4.95 | 4.95
 |  |  |  | 0
Preis Gesamt |  |  |  | 52.8

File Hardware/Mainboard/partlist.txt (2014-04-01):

Partlist

Exported from Mainboard.sch at 16.10.2013 17:04:55

EAGLE Version 6.1.0 Copyright (c) 1988-2012 CadSoft

Assembly variant: 

Part     Value             Device            Package                 Library           Sheet

ACTLED                     LEDCHIPLED_0805   CHIPLED_0805            led               5
LINKLED                    LEDCHIPLED_0805   CHIPLED_0805            led               5
SPDLED                     LEDCHIPLED_0805   CHIPLED_0805            led               5
LED1                       LEDSML0805        SML0805                 led               2
LED2                       LEDSML0805        SML0805                 led               2
---
C3       3n3               C-EUC0805         C0805                   rcl               1
---
C5       100µ              CPOL-EUUD-6,3X7,7 UD-6,3X7,7_NICHICON     rcl               1
C6       100µ              CPOL-EUUD-6,3X7,7 UD-6,3X7,7_NICHICON     rcl               1
---
C8       1µ                C-EUC0805         C0805                   rcl               2
---
C16      2µ2               C-EUC0805         C0805                   rcl               2
---
C17      1n                C-EUC0805         C0805                   rcl               2
---
C19      10p               C-EUC0805         C0805                   rcl               2
C20      10p               C-EUC0805         C0805                   rcl               2
---
C21      10µ               C-EUC0805         C0805                   rcl               4
C22      10µ               C-EUC0805         C0805                   rcl               4
---
C23      47µ               C-EUC0805         C0805                   rcl               4
C24      47µ               C-EUC0805         C0805                   rcl               4
---
C51      4µ7               C-EUC0805         C0805                   rcl               5
---
C52      18p               C-EUC0805         C0805                   rcl               5
C53      18p               C-EUC0805         C0805                   rcl               5
---
D1       1N4148            DIODE-SOD123      SOD123                  diode             1
---
D2       MBRS340T3         MBRS340T3         SMC                     diode             1
---
IC1      LT1763CDE-3.3     LT1763CDE-3.3     DFN12                   linear-technology 1
---
IC2      MAX3232CSE        MAX3232CSE        SO16                    maxim             3
---
NEED! Find!>>>>>>>>>>>>>>>>>>>L1       5µ                PIS4720           PIS4720                 inductor-fastron  1
---
Q1       16M               CRYSTALSM49       SM49                    crystal           2
---
Q2       25Mhz (1842313RL) CRYSTALHC49UP     HC49UP                  crystal           5
---
R1       5k6               R-EU_R0805        R0805                   rcl               1
R2       5k6               R-EU_R0805        R0805                   rcl               1
---

>>>>>>>>>>>>>>>>>>>>>>>>>>>>>>R3                         R-EU_R0805        R0805                   rcl               2
>>>>>>>>>>>>>>>>>>>>>>>>>>>>>>R38                        R-EU_R0805        R0805                   rcl               2
>>>>>>>>>>>>>>>>>>>>>>>>>>>>>>R39                        R-EU_R0805        R0805                   rcl               2
---
R49      330R              R-EU_R0805        R0805                   rcl               5
R50      330R              R-EU_R0805        R0805                   rcl               5
R51      330R              R-EU_R0805        R0805                   rcl               5

R54      12k4 1%           R-EU_R0805        R0805                   rcl               5
---
R55      1M                R-EU_R0805        R0805                   rcl               5
---
R56      49R9              R-EU_R0805        R0805                   rcl               5
R57      49R9              R-EU_R0805        R0805                   rcl               5
R58      49R9              R-EU_R0805        R0805                   rcl               5
R59      49R9              R-EU_R0805        R0805                   rcl               5
---
R60      10R               R-EU_R0805        R0805                   rcl               5
---
U$1      LT1376            LT1376            SOIC8                   Hardware          1
U$2      TM4C1233H6PM      TM4C1233H6PM      QFP50P1200X1200X160-64N Hardware          2
U$3      L6470HPOWERSO36   L6470HPOWERSO36   SOP65P1400X360-37N      Hardware          4
U$4      L6470HPOWERSO36   L6470HPOWERSO36   SOP65P1400X360-37N      Hardware          4
U$5      L6470HPOWERSO36   L6470HPOWERSO36   SOP65P1400X360-37N      Hardware          4
U$6      L6470HPOWERSO36   L6470HPOWERSO36   SOP65P1400X360-37N      Hardware          4
U$7      L6470HPOWERSO36   L6470HPOWERSO36   SOP65P1400X360-37N      Hardware          4
U$8      L6470HPOWERSO36   L6470HPOWERSO36   SOP65P1400X360-37N      Hardware          4
U$19     W5500             W5500             LQFP48                  Hardware          5<<<<<<<<<<<<<<
---
X29      057-006-1         057-006-1         057-006-1               con-panduit       2
X15      057-006-1         057-006-1         057-006-1               con-panduit       2
---
X16                        F09HPS            F09HP                   con-subd          3 unsicher,welcher?
---
X27      J1006F21          J1006F21          J1                      con-pulse         5
---
C4       100n              C-EUC0805         C0805                   rcl               1
C9       100n              C-EUC0805         C0805                   rcl               2
C10      100n              C-EUC0805         C0805                   rcl               2
C11      100n              C-EUC0805         C0805                   rcl               2
C12      100n              C-EUC0805         C0805                   rcl               2
C13      100n              C-EUC0805         C0805                   rcl               2
C14      100n              C-EUC0805         C0805                   rcl               2
C15      100n              C-EUC0805         C0805                   rcl               2
C38      100n              C-EUC0805         C0805                   rcl               3
C39      100n              C-EUC0805         C0805                   rcl               3
C40      100n              C-EUC0805         C0805                   rcl               3
C41      100n              C-EUC0805         C0805                   rcl               3
C42      100n              C-EUC0805         C0805                   rcl               3
C43      100n              C-EUC0805         C0805                   rcl               5
C44      100n              C-EUC0805         C0805                   rcl               5
C45      100n              C-EUC0805         C0805                   rcl               5
C46      100n              C-EUC0805         C0805                   rcl               5
C47      100n              C-EUC0805         C0805                   rcl               5
C48      100n              C-EUC0805         C0805                   rcl               5
C49      100n              C-EUC0805         C0805                   rcl               5
C50      100n              C-EUC0805         C0805                   rcl               5
C54      100n              C-EUC0805         C0805                   rcl               5
---
X28                        W237-02P          W237-132                con-wago-508      1 >>>> Gibts nicht bei Farnell
X1                         W237-02P          W237-132                con-wago-508      1
X2                         W237-02P          W237-132                con-wago-508      4
X3                         W237-02P          W237-132                con-wago-508      4
X4                         W237-02P          W237-132                con-wago-508      4
X5                         W237-02P          W237-132                con-wago-508      4
X6                         W237-02P          W237-132                con-wago-508      4
X7                         W237-02P          W237-132                con-wago-508      4
X8                         W237-02P          W237-132                con-wago-508      4
X9                         W237-02P          W237-132                con-wago-508      4
X10                        W237-02P          W237-132                con-wago-508      4
X11                        W237-02P          W237-132                con-wago-508      4
X12                        W237-02P          W237-132                con-wago-508      4
X13                        W237-02P          W237-132                con-wago-508      4
X14                        W237-02P          W237-132                con-wago-508      4
X17                        W237-02P          W237-132                con-wago-508      3
X18                        W237-02P          W237-132                con-wago-508      3
X19                        W237-02P          W237-132                con-wago-508      3
X20                        W237-02P          W237-132                con-wago-508      3
X21                        W237-02P          W237-132                con-wago-508      3
X22                        W237-02P          W237-132                con-wago-508      3
X23                        W237-02P          W237-132                con-wago-508      3
X24                        W237-02P          W237-132                con-wago-508      3
X25                        W237-02P          W237-132                con-wago-508      3
X26                        W237-02P          W237-132                con-wago-508      3
---
R5       100k              R-EU_R0805        R0805                   rcl               4
R10      100k              R-EU_R0805        R0805                   rcl               3
R13      100k              R-EU_R0805        R0805                   rcl               3
R16      100k              R-EU_R0805        R0805                   rcl               3
R19      100k              R-EU_R0805        R0805                   rcl               3
R22      100k              R-EU_R0805        R0805                   rcl               3
R25      100k              R-EU_R0805        R0805                   rcl               3
R27      100k              R-EU_R0805        R0805                   rcl               3
R30      100k              R-EU_R0805        R0805                   rcl               3
R33      100k              R-EU_R0805        R0805                   rcl               3
R36      100k              R-EU_R0805        R0805                   rcl               3
---
R4       8k2               R-EU_R0805        R0805                   rcl               4
R6       8k2               R-EU_R0805        R0805                   rcl               3
R7       8k2               R-EU_R0805        R0805                   rcl               4
R9       8k2               R-EU_R0805        R0805                   rcl               3
R11      8k2               R-EU_R0805        R0805                   rcl               3
R12      8k2               R-EU_R0805        R0805                   rcl               3
R14      8k2               R-EU_R0805        R0805                   rcl               3
R15      8k2               R-EU_R0805        R0805                   rcl               3
R17      8k2               R-EU_R0805        R0805                   rcl               3
R18      8k2               R-EU_R0805        R0805                   rcl               3
R20      8k2               R-EU_R0805        R0805                   rcl               3
R21      8k2               R-EU_R0805        R0805                   rcl               3
R23      8k2               R-EU_R0805        R0805                   rcl               3
R24      8k2               R-EU_R0805        R0805                   rcl               3
R26      8k2               R-EU_R0805        R0805                   rcl               3
R28      8k2               R-EU_R0805        R0805                   rcl               3
R29      8k2               R-EU_R0805        R0805                   rcl               3
R31      8k2               R-EU_R0805        R0805                   rcl               3
R32      8k2               R-EU_R0805        R0805                   rcl               3
R34      8k2               R-EU_R0805        R0805                   rcl               3
R35      8k2               R-EU_R0805        R0805                   rcl               3
R37      8k2               R-EU_R0805        R0805                   rcl               3
---
U$9      IL217AT           IL217AT           SOIC8                   Hardware          3
U$10     IL217AT           IL217AT           SOIC8                   Hardware          3
U$11     IL217AT           IL217AT           SOIC8                   Hardware          3
U$12     IL217AT           IL217AT           SOIC8                   Hardware          3
U$13     IL217AT           IL217AT           SOIC8                   Hardware          3
U$14     IL217AT           IL217AT           SOIC8                   Hardware          3
U$15     IL217AT           IL217AT           SOIC8                   Hardware          3
U$16     IL217AT           IL217AT           SOIC8                   Hardware          3
U$17     IL217AT           IL217AT           SOIC8                   Hardware          3
U$18     IL217AT           IL217AT           SOIC8                   Hardware          3
U$24     IL217AT           IL217AT           SOIC8                   Hardware          4
---
C27      220n              C-EUC0805         C0805                   rcl               4
C29      220n              C-EUC0805         C0805                   rcl               4
C33      220n              C-EUC0805         C0805                   rcl               4
C31      220n              C-EUC0805         C0805                   rcl               4
C35      220n              C-EUC0805         C0805                   rcl               4
C37      220n              C-EUC0805         C0805                   rcl               4
---
C7       10n               C-EUC0805         C0805                   rcl               1
C26      10n               C-EUC0805         C0805                   rcl               4
C30      10n               C-EUC0805         C0805                   rcl               4
C32      10n               C-EUC0805         C0805                   rcl               4
C34      10n               C-EUC0805         C0805                   rcl               4
C36      10n               C-EUC0805         C0805                   rcl               4
C28      10n               C-EUC0805         C0805                   rcl               4
C55      10n               C-EUC0805         C0805                   rcl               5
---
C18      4µ7               CPOL-EUUD-6,3X7,7 UD-6,3X7,7_NICHICON     rcl               1
---

C1       4µ7               C-EUC0805         C0805                   rcl               1
C2       4µ7               C-EUC0805         C0805                   rcl               1
---
C56                        C-EUC1210         C1210                   rcl               3 <<<<<<<<<<<<<<<<<<<<<<<< eyo .. Werte noch rausfinden
C57                        C-EUC1210         C1210                   rcl               3
C58                        C-EUC1210         C1210                   rcl               3
C59                        C-EUC1210         C1210                   rcl               3
C60                        C-EUC1210         C1210                   rcl               3
C61                        C-EUC1210         C1210                   rcl               3
C62                        C-EUC1210         C1210                   rcl               3
C63                        C-EUC1210         C1210                   rcl               3
C64                        C-EUC1210         C1210                   rcl               3
C65                        C-EUC1210         C1210                   rcl               3
---
C66                        C-EUC1210         C1210                   rcl               4
C67                        C-EUC1210         C1210                   rcl               4
C68                        C-EUC1210         C1210                   rcl               4
C69                        C-EUC1210         C1210                   rcl               4
C70                        C-EUC1210         C1210                   rcl               4
C71                        C-EUC1210         C1210                   rcl               4
C72                        C-EUC1210         C1210                   rcl               4
---
R40      10k               R-EU_R0805        R0805                   rcl               5
R41      10k               R-EU_R0805        R0805                   rcl               5
R42      10k               R-EU_R0805        R0805                   rcl               5
R43      10k               R-EU_R0805        R0805                   rcl               5
R44      10k               R-EU_R0805        R0805                   rcl               5
R45      10k               R-EU_R0805        R0805                   rcl               5
R46      10k               R-EU_R0805        R0805                   rcl               5
R47      10k               R-EU_R0805        R0805                   rcl               5
R48      10k               R-EU_R0805        R0805                   rcl               5
R52      10k               R-EU_R0805        R0805                   rcl               5
R53      10k               R-EU_R0805        R0805                   rcl               5
---
D3        HSMS-2802-TR1G   DIODE_2CACA-SOT23 SOT23                   diode             4
D4        HSMS-2802-TR1G   DIODE_2CACA-SOT23 SOT23                   diode             4
D5        HSMS-2802-TR1G   DIODE_2CACA-SOT23 SOT23                   diode             4
D6        HSMS-2802-TR1G   DIODE_2CACA-SOT23 SOT23                   diode             4
D7        HSMS-2802-TR1G   DIODE_2CACA-SOT23 SOT23                   diode             4
D8        HSMS-2802-TR1G   DIODE_2CACA-SOT23 SOT23                   diode             4
---

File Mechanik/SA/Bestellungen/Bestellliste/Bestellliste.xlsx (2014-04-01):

 | Stückzahl | Bezeichnung | Artikelnummer | Preis/Stück | Gesamt | Zusatz | Webadresse
 |  |  |  |  | 0
Rahmen + Profile +Zubehör | 600 | L-Profile Aluminium |  |  | 357.5 | Angebot siehe Anhang | http://www.3d-alu.de/
 | 1 | Profil 20x20,4H,leicht,plan | 1.10.020020.43LP.60 | 31.07 | 31.07
 | 4 | Profil 40x40,4E,leicht,plan | 1.11.040040.43L.60 | 70.53 | 282.12
 | 5 | Profil 20x40,6H,leicht,plan | 1.10.020040.64LP.60 | 52.58 | 262.9
 |  |  |  |  | 0
 |  |  |  |  | 0
 |  |  |  |  | 0
Z-Achse | 2 | Linearführung | SSVR24-280 | 74.05 | 148.1 |  | www.misumi.de
 | 1 | Führungswagen | BNFA1004C-30 | 38.5 | 38.5 |  | www.misumi.de
 | 1 | Loslager | BUV8 | 22 | 22 |  | www.misumi.de
 | 1 | Festlager | BSV8S | 70.5 | 70.5 |  | www.misumi.de
 | 1 | Kugelgewindetriebe | BSSC1004-280-SWC5 | 125.4 | 125.4 |  | www.misumi.de
 | 1 | Kupplung | MCO15-5-6 | 11.3 | 11.3 |  | www.misumi.de
X-Achse | 2 | Linearführung | SVRN28-820 | 117.88 | 235.76 |  | www.misumi.de
 | 1 | Kugelgewindetriebe | BSSC1510-835-SWC7 | 156 | 156 |  | www.misumi.de
 | 1 | Loslager | BUV12 | 28 | 28 |  | www.misumi.de
 | 1 | Festlager | BSV12 | 63.3 | 63.3 |  | www.misumi.de
 | 1 | Führungswagen | BNFA1510C-30 | 43.2 | 43.2 |  | www.misumi.de
 | 1 | Kupplung | MCO20-6.35-10 | 13.1 | 13.1 |  | www.misumi.de
 | 1 | Motor | ST5918X1008-A | 34.2 | 34.2 |  | www.de.naotec.com
 |  |  |  |  | 0
Y-Achse | 4 | Linearführung | SVRL28-1700 | 198.44 | 793.76 |  | www.misumi.de
 | 2 | Kugelgewindetriebe | BSSC2010-1670-SWC7 | 216.6 | 433.2 |  | www.misumi.de
 | 2 | Loslager | BUV15 | 29.5 | 59 |  | www.misumi.de
 | 2 | Festlager | BSV15 | 74.1 | 148.2 |  | www.misumi.de
 | 2 | Führungsmutter | BNFA2010C-30 | 49 | 98 |  | www.misumi.de
 | 2 | Kupplung | MCO20-6.35-12 | 13.1 | 26.2 |  | www.misumi.de
 | 2 | Motor | ST5918L1008-A | 57.9 | 115.8 |  | www.de.nanotec.com
 |  |  |  |  | 0
Greifer | 2 | Rillenkugellager | 16002 FAG | 5.04 | 10.08 |  | http://www.ekugellager.de/advanced_search_result.php?keywords=16002&W%E4lzlager-Suche=Artikel+suchen
 | 1 | Zylinderrollenlager | N202-E-TVP2 FAG | 30.68 | 30.68 |  | http://www.ekugellager.de/advanced_search_result.php?W%E4lzlager-Suche=Artikel+suchen
 | 3 | Schrittmotor | PSM42BYGHW603 | 15.95 | 47.85 |  | http://www.pollin.de/shop/dt/NjQ1OTg2OTk-/Motoren/Schrittmotoren/Schrittmotor_PSM42BYGHW603_1_8_.html
 | 1 | Linearkugellager | LMK12 | 5.04 | 5.04 |  | http://de.misumi-ec.com/eu/ItemDetail/10302037730.html
 | 1 | FührungsWelle | PSFRM12-145.0-F28.0-B17-P8-T31.0-S17-Q8 | 12.8 | 12.8 |  | http://de.misumi-ec.com/eu/ItemDetail/10300087260.html
 | 1 | Trapezgewindetriebe | MTSRX20-221-F17-V12-T11-G8-Q15-S40-E12 | 54.7 | 54.7 |  | http://de.misumi-ec.com/eu/ItemDetail/10300083330.html
 | 1 | Spindelmutter | MTSPNR20 | 51.4 | 51.4 |  | http://de.misumi-ec.com/eu/ItemDetail/10300085070.html
 | 1 | Zahnrad | 416-010-0022 | 3.1 | 3.1 | Stahl ungehärtet | http://www.gg-antriebstechnik.de/
 | 1 | Zahnrad | 416-010-0066 | 12.8 | 12.8 | Stahl ungehärtet | http://www.gg-antriebstechnik.de/
 | 1 | Zahnrad | 416-010-0014 | unbekannt (geschätz 3 Euro) | 3 | Stahl ungehärtet | http://www.gg-antriebstechnik.de/
 | 1 | Zahnrad | 416-010-0070 | unbekannt ( geschätzt 15 Euro) | 15 | Stahl ungehärtet | http://www.gg-antriebstechnik.de/
Boxen | 850 | kleine Box (rot) | KSS 54 54 45 | 0.17 | 144.5 | ab 22.11 verfügbar | http://www.befestigungsfuchs.de/Betriebsbedarf/Aufbewahrung-Ordnung/Sortimentskasten-Sortimentsboxen/Zubehoer/1-Box-54x54x45-mm-fuer-Stahlblech-Sortimentskast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
 | 100 | mittlere Box (gelb) | KSS 54 108 45 | 0.22 | 22 |  | http://www.befestigungsfuchs.de/Betriebsbedarf/Aufbewahrung-Ordnung/Sortimentskasten-Sortimentsboxen/Zubehoer/1-Box-54x108x45-mm-fuer-Stahlblech-Sortimentskas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
 | 100 | große Box (blau) | KSS 108 108 45 | 0.38 | 38 |  | http://www.befestigungsfuchs.de/Betriebsbedarf/Aufbewahrung-Ordnung/Sortimentskasten-Sortimentsboxen/Zubehoer/1-Box-108x108x45-mm-fuer-Stahlblech-Sortimentska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
 |  |  |  |  | 0
 |  |  |  |  | 0
Elektronik | 5 | Mikroschalter | 699-4664 | 1.92 | 9.6 |  | http://de.rs-online.com/web/p/mikroschalter/6994664/
 |  |  |  |  | 0
Summe |  |  |  |  | 4057.66

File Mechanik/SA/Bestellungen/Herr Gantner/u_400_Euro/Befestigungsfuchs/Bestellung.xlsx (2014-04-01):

Bezeichnung | Stück | Artikelnummer | Preis/Stück | Preis | Zusatz | URL
kleine Box (rot) | 750 | KSS 54 54 45 | 0.17 | 127.5 | ab 22.11 wieder verfügbar | http://www.befestigungsfuchs.de/Betriebsbedarf/Aufbewahrung-Ordnung/Sortimentskasten-Sortimentsboxen/Zubehoer/1-Box-54x54x45-mm-fuer-Stahlblech-Sortimentskast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
mittlere Box (gelb) | 100 | KSS 54 108 45 | 0.22 | 22 |  | http://www.befestigungsfuchs.de/Betriebsbedarf/Aufbewahrung-Ordnung/Sortimentskasten-Sortimentsboxen/Zubehoer/1-Box-54x108x45-mm-fuer-Stahlblech-Sortimentskas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
große Box (blau) | 100 | KSS 108 108 45 | 0.38 | 38 |  | http://www.befestigungsfuchs.de/Betriebsbedarf/Aufbewahrung-Ordnung/Sortimentskasten-Sortimentsboxen/Zubehoer/1-Box-108x108x45-mm-fuer-Stahlblech-Sortimentska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
 |  |  |  | 0
 |  |  |  | 0
 |  |  |  | 0
 |  |  |  | 0 | zzgl. Versandkosten
Preis Gesamt |  |  |  | 187.5

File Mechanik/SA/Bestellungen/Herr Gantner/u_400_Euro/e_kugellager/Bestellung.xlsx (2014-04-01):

Bezeichnung | Stück | Artikelnummer | Preis/Stück | Preis | Zusatz | URL
Rillenkugellager | 2 | 16002 FAG | 5.04 | 10.08 |  | http://www.ekugellager.de/advanced_search_result.php?keywords=16002&W%E4lzlager-Suche=Artikel+suchen
Zylinderrollenlager | 1 | N202-E-TVP2 FAG | 30.68 | 30.68 |  | http://www.ekugellager.de/advanced_search_result.php?W%E4lzlager-Suche=Artikel+suchen
 |  |  |  | 0
 |  |  |  | 0
 |  |  |  | 0
 |  |  |  | 0
 |  |  |  | 0 | Versand fehlt noch!
Preis Gesamt |  |  |  | 40.76

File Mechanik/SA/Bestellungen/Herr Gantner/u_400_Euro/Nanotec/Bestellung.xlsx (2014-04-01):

Bezeichnung | Stück | Artikelnummer | Preis/Stück | Preis | Zusatz | URL
Schrittmotor | 1 | ST5918X1008-A | 34.02 | 34.02 |  | www.nanotec.de
Schrittmotor | 2 | ST5918L1008-A | 57.9 | 115.8
 |  |  |  | 0
 |  |  |  | 0
 |  |  |  | 0
 |  |  |  | 0
 |  |  |  | 0 | zzgl. Versandkosten
Preis Gesamt |  |  |  | 149.82

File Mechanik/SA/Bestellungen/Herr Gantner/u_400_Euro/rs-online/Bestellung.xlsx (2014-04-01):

Bezeichnung | Stück | Artikelnummer | Preis/Stück | Preis | Zusatz | URL
Mikroschalter | 5 | 699-4664 | 1.92 | 9.6 |  | http://de.rs-online.com/web/p/mikroschalter/6994664/
 |  |  |  | 0
 |  |  |  | 0
 |  |  |  | 0
 |  |  |  | 0
 |  |  |  | 0
 |  |  |  | 0 | zzgl. Versandkosten
Preis Gesamt |  |  |  | 9.6

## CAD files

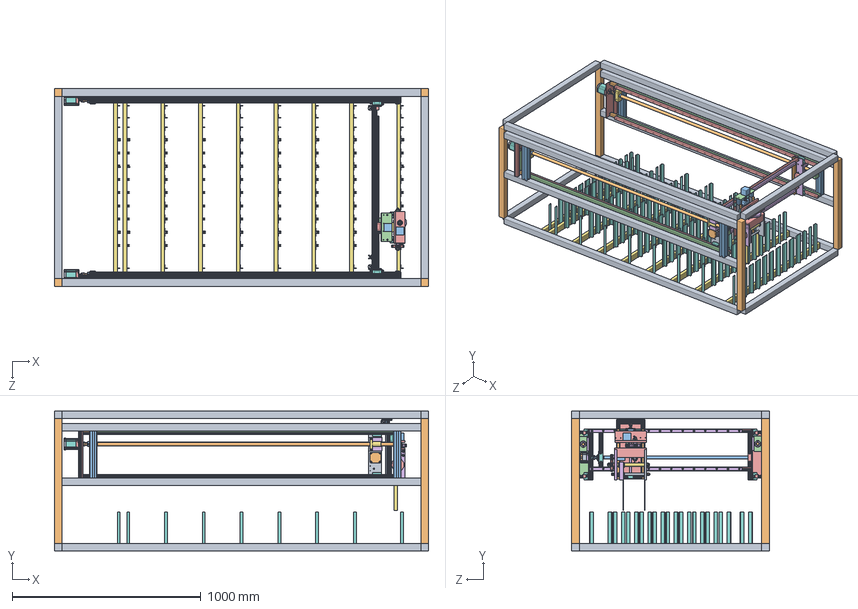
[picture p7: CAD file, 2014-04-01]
Mechanik/SA/Solid_Works/Bauteileautomat.SLDASM
1980.0 x 740.0 x 1045.6 mm
bosch_3842993120_2dhdbkbtd5fyfxp6933e5ukc1 x 8
bosch_3842993120_dp0mewckhth7llxp48xku9oe7 x 4
x.2
bnfb1510c_30_2_14b
x.2.1.1.1 x 2
bosch_3842992888_wz7no3yknb5kp3apgrcfn1yc x 3
bosch_3842992888_1m6r2ig9ogbvhzgamjmk3rfan x 2
bosch_3842992888_57t4u2t094ehub5wmplcmm95a x 2
a
b
c
d
e
f
g
Schrittmotor x 3
Halterung_Motor_Z_Achse
Platte
bnfb1004c_30_2_14b
Halterung_statisch
Spannscheibe_Achse x 2
Spannscheibe_Welle x 3
mutter_din_937-m12-kk-14h_-_au x 3
Haltearm_Drehgelenk2
Halterung_Motor
inafag_n202-e-tvp2_aqqhrrap8qdp81ymy9u0uz87v_01
inafag_n202-e-tvp2_aqqhrrap8qdp81ymy9u0uz87v_02
inafag_n202-e-tvp2_aqqhrrap8qdp81ymy9u0uz87v_03
inafag_n202-e-tvp2_aqqhrrap8qdp81ymy9u0uz87v_04
inafag_n202-e-tvp2_aqqhrrap8qdp81ymy9u0uz87v_05
inafag_n202-e-tvp2_aqqhrrap8qdp81ymy9u0uz87v_06
inafag_n202-e-tvp2_aqqhrrap8qdp81ymy9u0uz87v_07
Führungsarm
Greifarm x 2
din_en_iso_7046-2_m4x8_h_1 x 4
mutter_din_937-m16-kk-14h_-_au
din_en_iso_7046-2_m6x25_h_1 x 4
mtspnr20_2_14b
Halterung Zahnrrad
Welle_bestellt
lmk12_2_14b
Achse_neu
mutter_din_en_24032-m8-6 x 4
Welle_drehgelenk_neu
Motorhalterung
inafag_16002_9gwbvro1p7ifqmz6650knblzl_01 x 2
inafag_16002_9gwbvro1p7ifqmz6650knblzl_02 x 2
inafag_16002_9gwbvro1p7ifqmz6650knblzl_03 x 2
inafag_16002_9gwbvro1p7ifqmz6650knblzl_04 x 2
inafag_16002_9gwbvro1p7ifqmz6650knblzl_05 x 2
inafag_16002_9gwbvro1p7ifqmz6650knblzl_06 x 2
inafag_16002_9gwbvro1p7ifqmz6650knblzl_07 x 2
inafag_16002_9gwbvro1p7ifqmz6650knblzl_08 x 2
inafag_16002_9gwbvro1p7ifqmz6650knblzl_09 x 2
inafag_16002_9gwbvro1p7ifqmz6650knblzl_10 x 2
inafag_16002_9gwbvro1p7ifqmz6650knblzl_11 x 2
y.1 x 2
y.3 x 2
y.1.1.1 x 2
y.2.1.1 x 2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

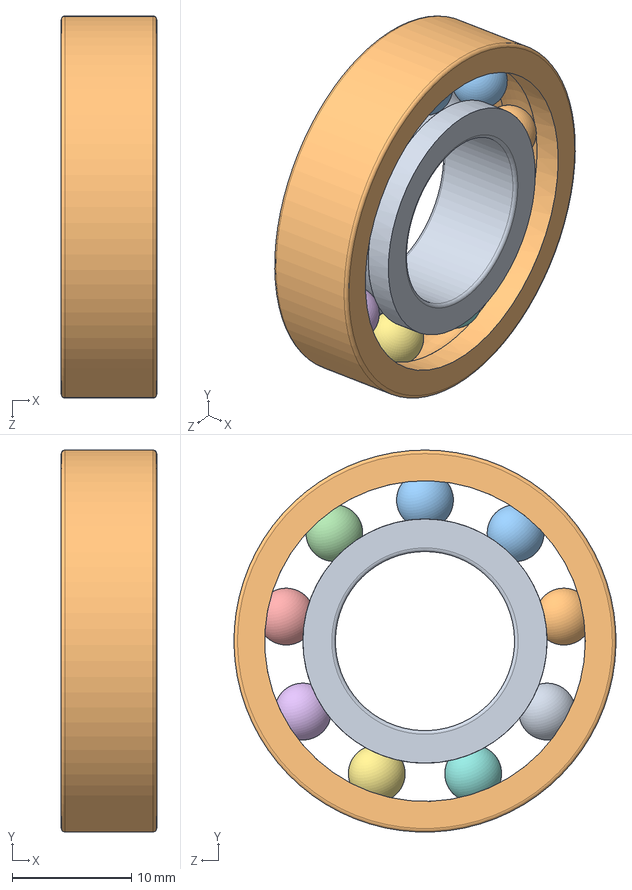
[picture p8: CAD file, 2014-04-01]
Mechanik/SA/Solid_Works/Greifer/Festlager/inafag_16002_9gwbvro1p7ifqmz6650knblzl/inafag_16002_9gwbvro1p7ifqmz6650knblzl.SLDASM
8.00 x 32.0 x 32.0 mm
inafag_16002_9gwbvro1p7ifqmz6650knblzl_01
inafag_16002_9gwbvro1p7ifqmz6650knblzl_02
inafag_16002_9gwbvro1p7ifqmz6650knblzl_03
inafag_16002_9gwbvro1p7ifqmz6650knblzl_04
inafag_16002_9gwbvro1p7ifqmz6650knblzl_05
inafag_16002_9gwbvro1p7ifqmz6650knblzl_06
inafag_16002_9gwbvro1p7ifqmz6650knblzl_07
inafag_16002_9gwbvro1p7ifqmz6650knblzl_08
inafag_16002_9gwbvro1p7ifqmz6650knblzl_09
inafag_16002_9gwbvro1p7ifqmz6650knblzl_10
inafag_16002_9gwbvro1p7ifqmz6650knblzl_11

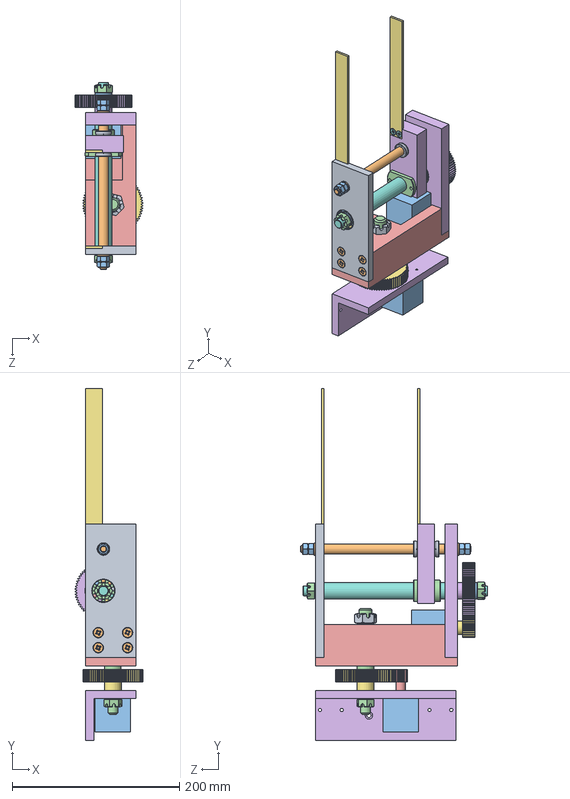
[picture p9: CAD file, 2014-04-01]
Mechanik/SA/Solid_Works/Greifer/Greifer.SLDASM
81.3 x 421.0 x 224.0 mm
Halterung_statisch
Spannscheibe_Achse x 2
Spannscheibe_Welle x 3
mutter_din_937-m12-kk-14h_-_au x 3
Haltearm_Drehgelenk2
Halterung_Motor
inafag_n202-e-tvp2_aqqhrrap8qdp81ymy9u0uz87v_01
inafag_n202-e-tvp2_aqqhrrap8qdp81ymy9u0uz87v_02
inafag_n202-e-tvp2_aqqhrrap8qdp81ymy9u0uz87v_03
inafag_n202-e-tvp2_aqqhrrap8qdp81ymy9u0uz87v_04
inafag_n202-e-tvp2_aqqhrrap8qdp81ymy9u0uz87v_05
inafag_n202-e-tvp2_aqqhrrap8qdp81ymy9u0uz87v_06
inafag_n202-e-tvp2_aqqhrrap8qdp81ymy9u0uz87v_07
Führungsarm
Greifarm x 2
din_en_iso_7046-2_m4x8_h_1 x 4
mutter_din_937-m16-kk-14h_-_au
din_en_iso_7046-2_m6x25_h_1 x 4
Schrittmotor x 2
mtspnr20_2_14b
Halterung Zahnrrad
Welle_bestellt
lmk12_2_14b
Achse_neu
mutter_din_en_24032-m8-6 x 4
Welle_drehgelenk_neu
Motorhalterung
inafag_16002_9gwbvro1p7ifqmz6650knblzl_01 x 2
inafag_16002_9gwbvro1p7ifqmz6650knblzl_02 x 2
inafag_16002_9gwbvro1p7ifqmz6650knblzl_03 x 2
inafag_16002_9gwbvro1p7ifqmz6650knblzl_04 x 2
inafag_16002_9gwbvro1p7ifqmz6650knblzl_05 x 2
inafag_16002_9gwbvro1p7ifqmz6650knblzl_06 x 2
inafag_16002_9gwbvro1p7ifqmz6650knblzl_07 x 2
inafag_16002_9gwbvro1p7ifqmz6650knblzl_08 x 2
inafag_16002_9gwbvro1p7ifqmz6650knblzl_09 x 2
inafag_16002_9gwbvro1p7ifqmz6650knblzl_10 x 2
inafag_16002_9gwbvro1p7ifqmz6650knblzl_11 x 2

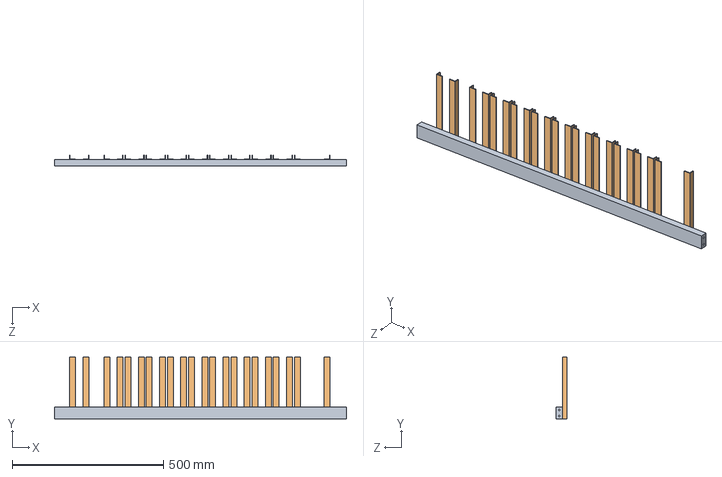
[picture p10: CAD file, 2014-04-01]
Mechanik/SA/Solid_Works/Rahmen/L-Profil_Querstange/L_profiel_Querstange.SLDASM
965.6 x 205.0 x 35.0 mm
bosch_3842992891_61lobwccewetiudy9n9t9uimi
L_Profil x 22

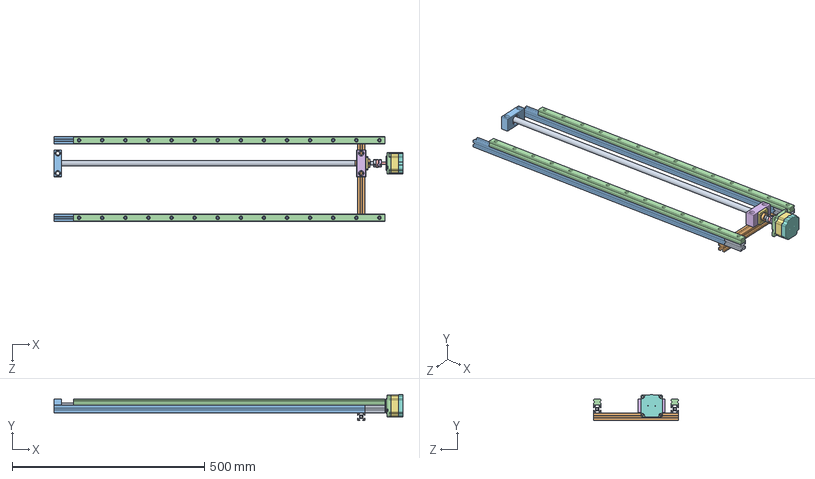
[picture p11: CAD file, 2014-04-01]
Mechanik/SA/Solid_Works/X-Achse/bssc1510_835_sc8_2_14b.SLDASM
906.6 x 67.9 x 221.5 mm
x.1
x.3
x.1.1.1
x.2.1.1
x.3.1.1
x.1.1
x.2.1
x.3.1
x.4.1
x.5.1
bosch_3842992888_9c9s6psdorxyhd1epp1jf78yp x 2
x.1.1.1.1 x 2
x.a
x.b
x.c
x.d
x.e
x.f
x.g
Frontcap_ST5918_1
shaft_forward_5709_1
Schrauben_ISO_7045_M3_1 x 4
Stator_5918_X
Endcap_5918_1
bosch_3842992888_7lia0498i12anehwyzh4p1fgc x 2
bosch_3842992888_dva00vq3akj3v9a29cw93lqum

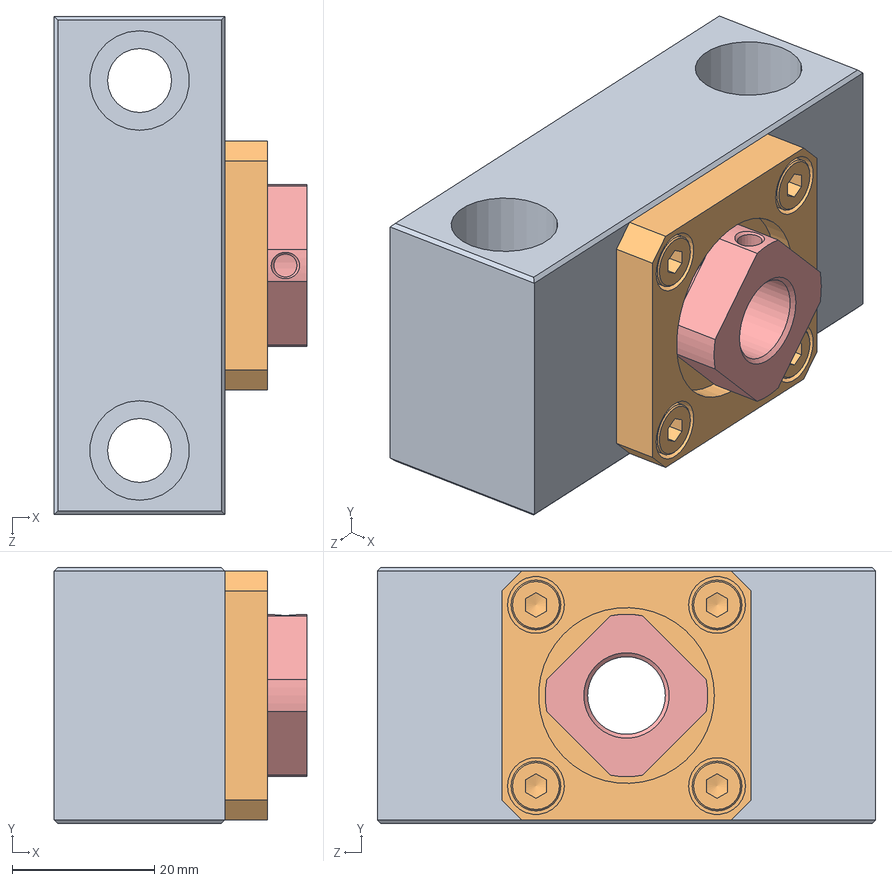
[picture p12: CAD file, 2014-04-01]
Mechanik/SA/Solid_Works/X-Achse/Festlager/bsv12_2_14b.SLDASM
35.5 x 36.0 x 70.0 mm
x.1.1
x.2.1
x.3.1
x.4.1
x.5.1

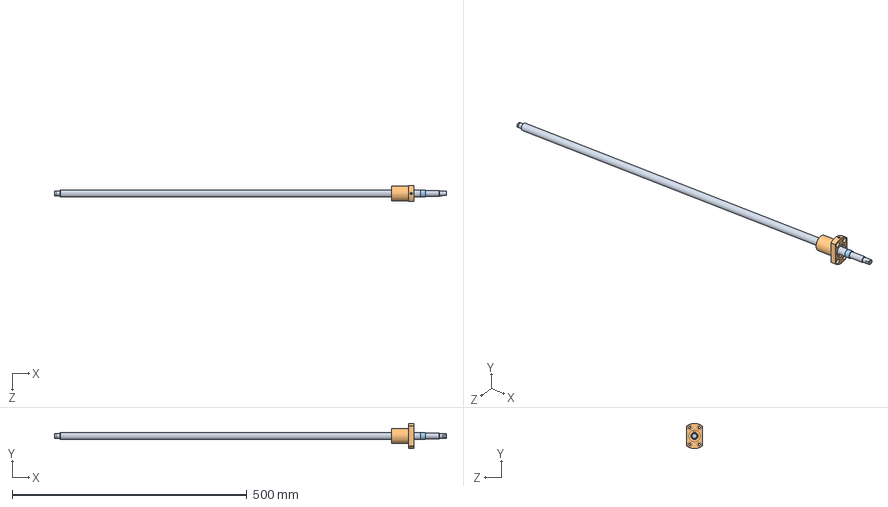
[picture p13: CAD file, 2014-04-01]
Mechanik/SA/Solid_Works/X-Achse/Gewindetribe_X_achse/bssc1510_835_sc8_2_14b.SLDASM
835.0 x 54.0 x 34.0 mm
x.1
x.2
x.3

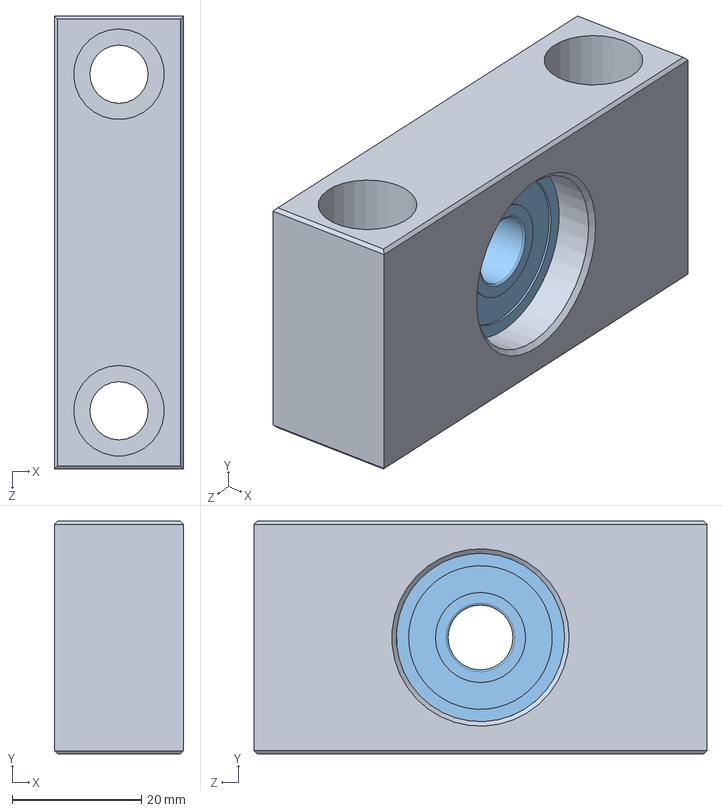
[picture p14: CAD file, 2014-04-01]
Mechanik/SA/Solid_Works/X-Achse/Loslager/buv12_2_14b.SLDASM
20.0 x 36.0 x 70.0 mm
x.1.1.1
x.2.1.1
x.3.1.1

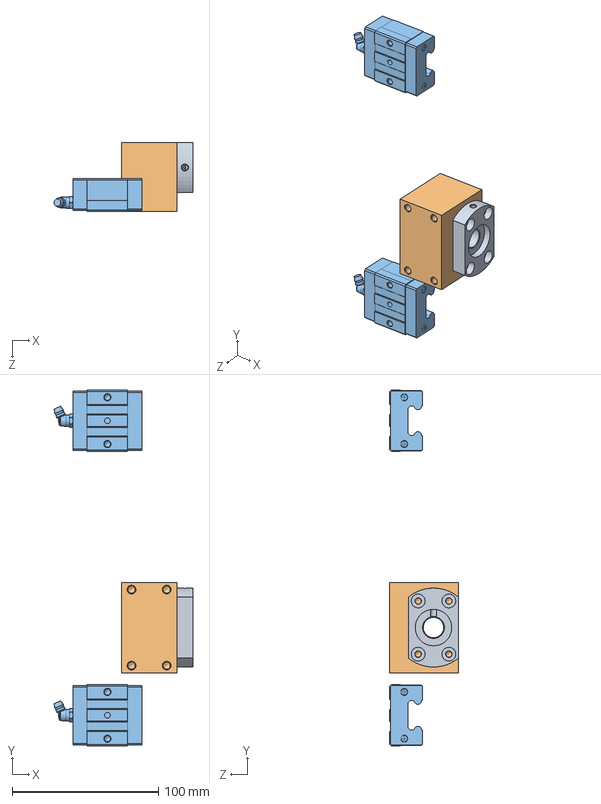
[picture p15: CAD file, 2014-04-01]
Mechanik/SA/Solid_Works/X-Achse/Schlitten/Schlitten_x-Achse.SLDASM
95.0 x 243.5 x 47.0 mm
x.2
bnfb1510c_30_2_14b
x.2.1.1.1 x 2

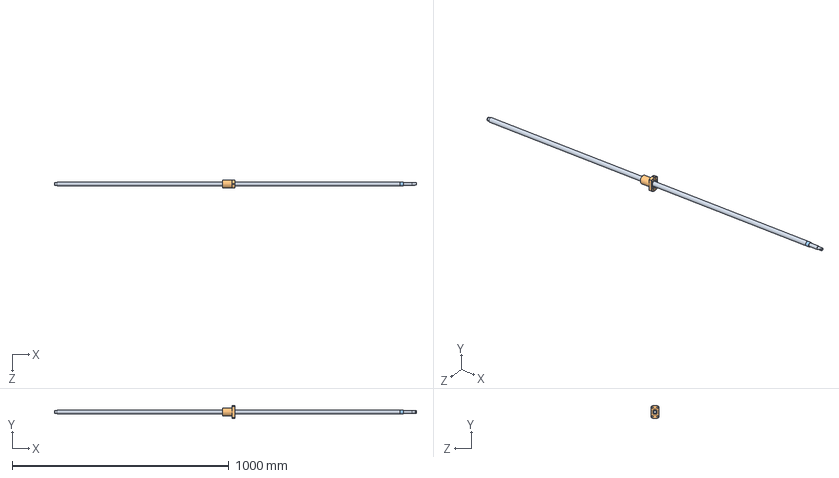
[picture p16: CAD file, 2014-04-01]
Mechanik/SA/Solid_Works/Y-Achse/Kugelgewindetriebe/bssc2010_1670_sc8_2_14b.SLDASM
1670.0 x 61.9 x 38.0 mm
y.1
y.2
y.3

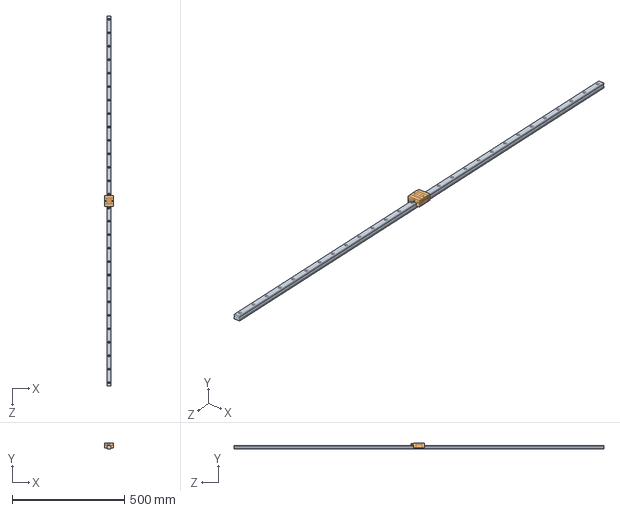
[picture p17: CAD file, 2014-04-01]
Mechanik/SA/Solid_Works/Y-Achse/Linearführungen/svrl28_1650_2_14b.SLDASM
42.0 x 28.0 x 1650.0 mm
y.1.1.1.1
y.2.1.1.1

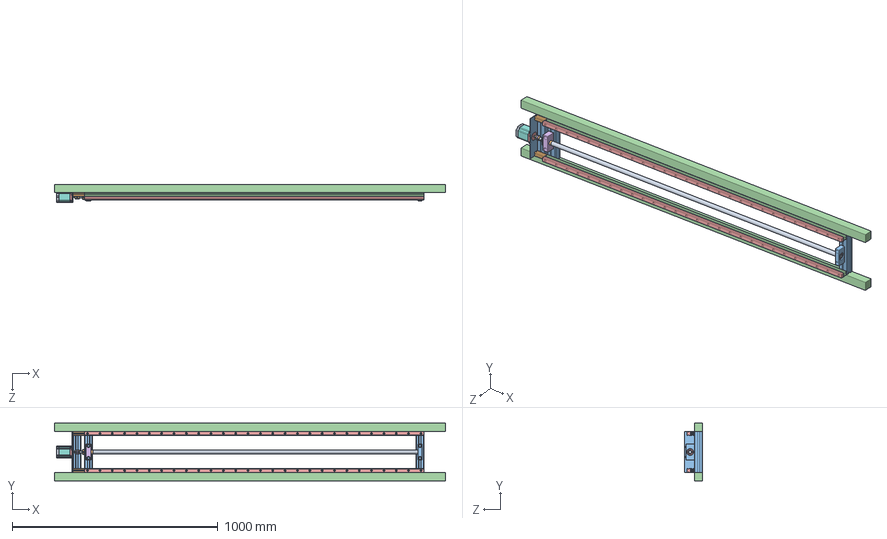
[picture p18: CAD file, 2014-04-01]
Mechanik/SA/Solid_Works/Y-Achse/Linke_seite.SLDASM
1900.0 x 280.0 x 89.2 mm
y.1
y.3
y.1.1.1
y.2.1.1
y.3.1.1
y.1.1
y.2.1
y.3.1
y.4.1
y.5.1
bosch_3842993120_6do5v09iy6ebk03fg871s10o3 x 3
bosch_3842992888_e3htx9vi1mc72io2jozt5vwey x 2
y.1.1.1.1 x 2
y.a
y.b
y.c
y.d
y.e
y.f
y.g
Frontcap_ST5918
shaft_forward_5709
Schrauben_ISO_7045_M3 x 4
Stator_5918_L
Endcap_5918
bosch_3842992888_aff6iaz91xwbgzhnykkapvmd0 x 2
Motorplatte_y.Achse
bosch_3842993120_2dhdbkbtd5fyfxp6933e5ukc1 x 2

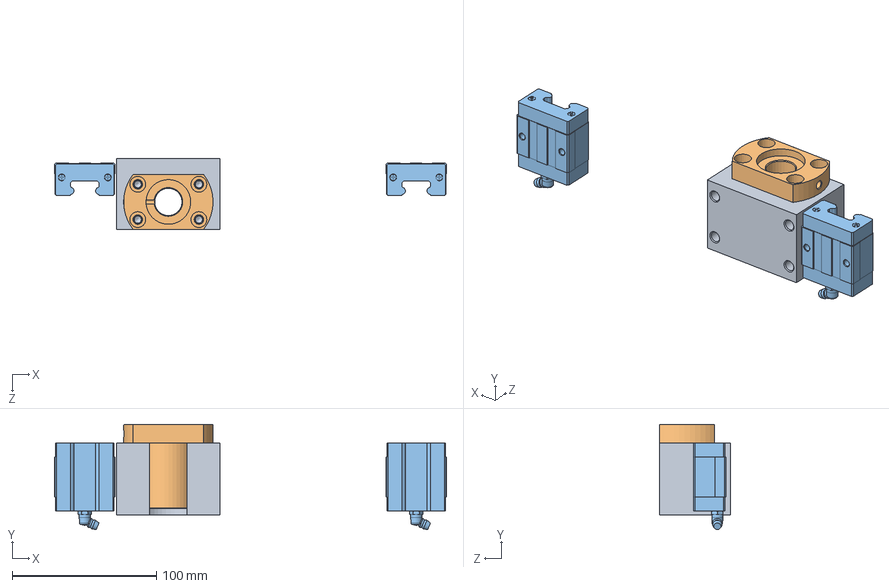
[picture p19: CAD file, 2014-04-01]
Mechanik/SA/Solid_Works/Y-Achse/Schlitten/Schlitten_y.Achse.SLDASM
272.0 x 73.0 x 49.0 mm
bnfb2010c_30_2_14b
y.2
y.2.1.1.1 x 2

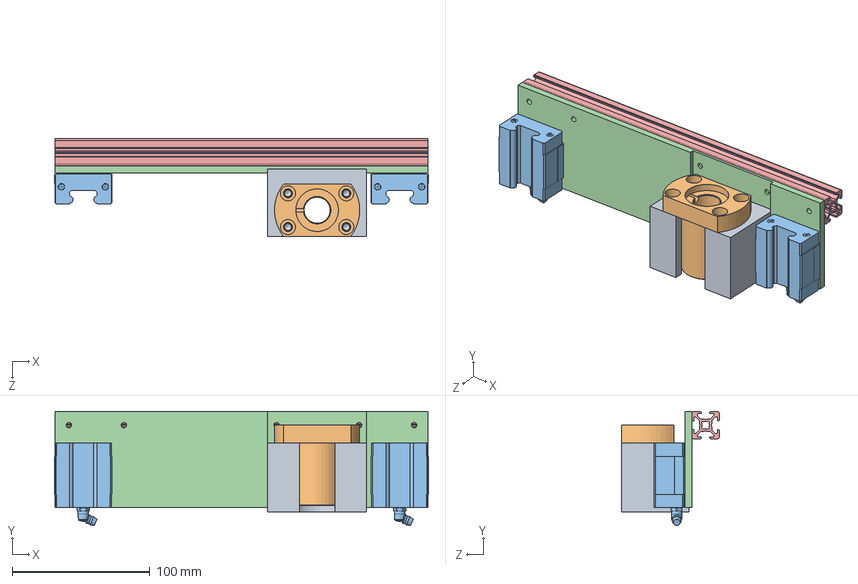
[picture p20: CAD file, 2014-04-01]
Mechanik/SA/Solid_Works/Y-Achse/Schlitten_rechts/Schlitten_y.achse_rechts.SLDASM
272.0 x 83.0 x 71.0 mm
bnfb2010c_30_2_14b
y.2
y.2.1.1.1 x 2
Befestigung_x_Achse_rechts
bosch_3842992888_kdlq4eelab0t8ykqr22w4puj

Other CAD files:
Mechanik/SA/Solid_Works/Rahmen/Automat.SLDASM
Mechanik/SA/Solid_Works/Y-Achse/Y-Achse_links/Y_links.SLDASM
Mechanik/SA/Solid_Works/Y-Achse/Y-achse_rechts/bssc2010_1670_sc8_2_14b.SLDASM
Mechanik/SA/Solid_Works/Z-Achse/Festlager/bsv8s_2_14b.SLDASM
Mechanik/SA/Solid_Works/Greifer/Achse/Achse.SLDPRT
Mechanik/SA/Solid_Works/Greifer/Achse/Achse_neu.SLDPRT
Mechanik/SA/Solid_Works/Greifer/Drehgelenk/Welle_Drehgelenk/Welle_Drehgelenk.SLDPRT
Mechanik/SA/Solid_Works/Greifer/Drehgelenk/Welle_Drehgelenk/Welle_drehgelenk_neu.SLDDRW
Mechanik/SA/Solid_Works/Greifer/Drehgelenk/Welle_Drehgelenk/Welle_drehgelenk_neu.SLDPRT
Mechanik/SA/Solid_Works/Greifer/Drehgelenk_Motor/Motor_Drehgelenk.SLDPRT
Mechanik/SA/Solid_Works/Greifer/Drehgelenk_Motorhalterung/Motorhalterung.SLDDRW
Mechanik/SA/Solid_Works/Greifer/Drehgelenk_Motorhalterung/Motorhalterung.SLDPRT
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

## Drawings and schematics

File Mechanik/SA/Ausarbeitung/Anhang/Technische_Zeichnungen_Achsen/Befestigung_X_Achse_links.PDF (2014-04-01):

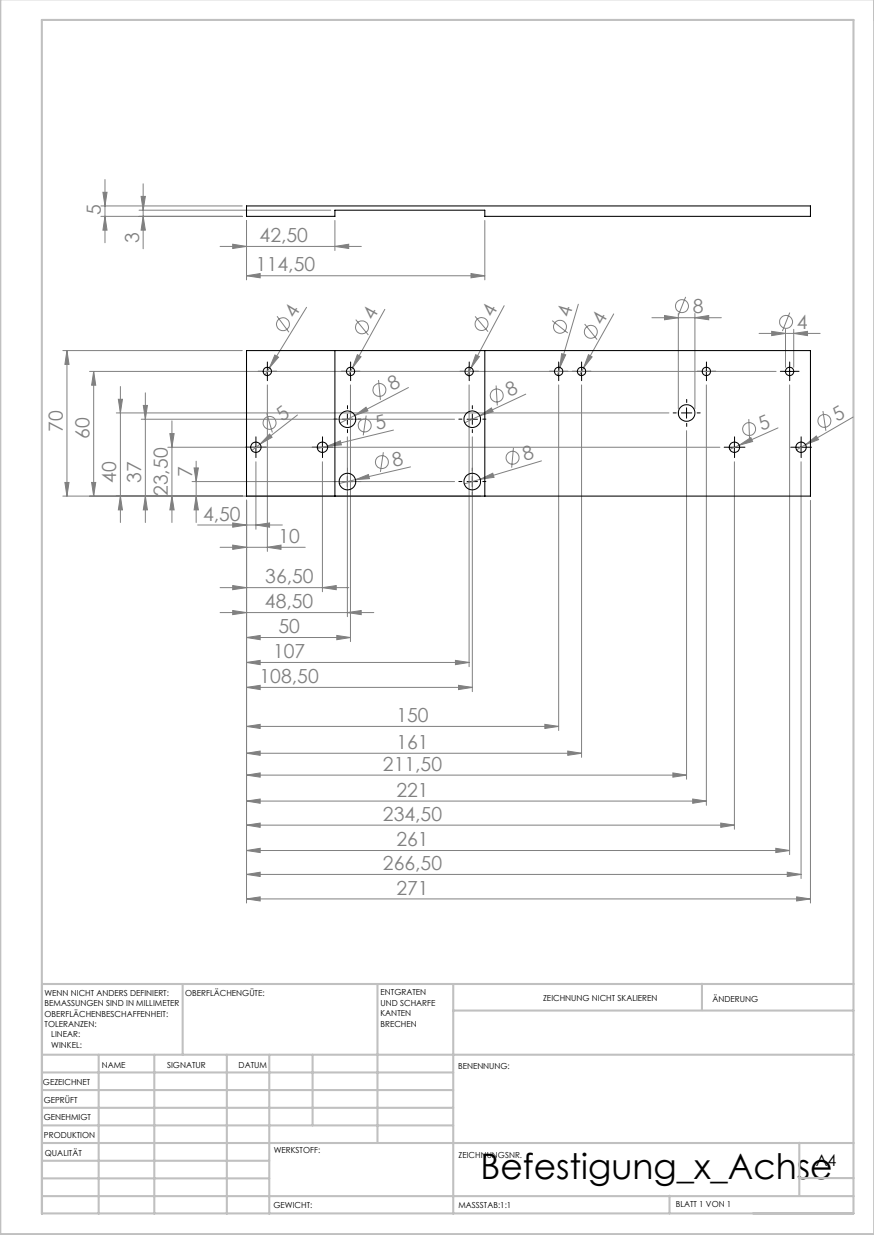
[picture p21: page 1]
MASSSTAB:1:1; BLATT 1 VON 1; ZEICHNUNG NICHT SKALIEREN; ÄNDERUNG; UND SCHARFE; WENN NICHT ANDERS DEFINIERT:; OBERFLÄCHENGÜTE:

BEMASSUNGEN SIND IN MILLIMETER
OBERFLÄCHENBESCHAFFENHEIT:
TOLERANZEN:
LINEAR:
WINKEL:

NAME | SIGNATUR | DATUM | | | | BENENNUNG:
QUALITÄT | | | | WERKSTOFF: | Befestigung_x_Achse GEWICHT: ZEICHNUNGSNR. | A4

GEZEICHNET
GEPRÜFT
GENEHMIGT
PRODUKTION

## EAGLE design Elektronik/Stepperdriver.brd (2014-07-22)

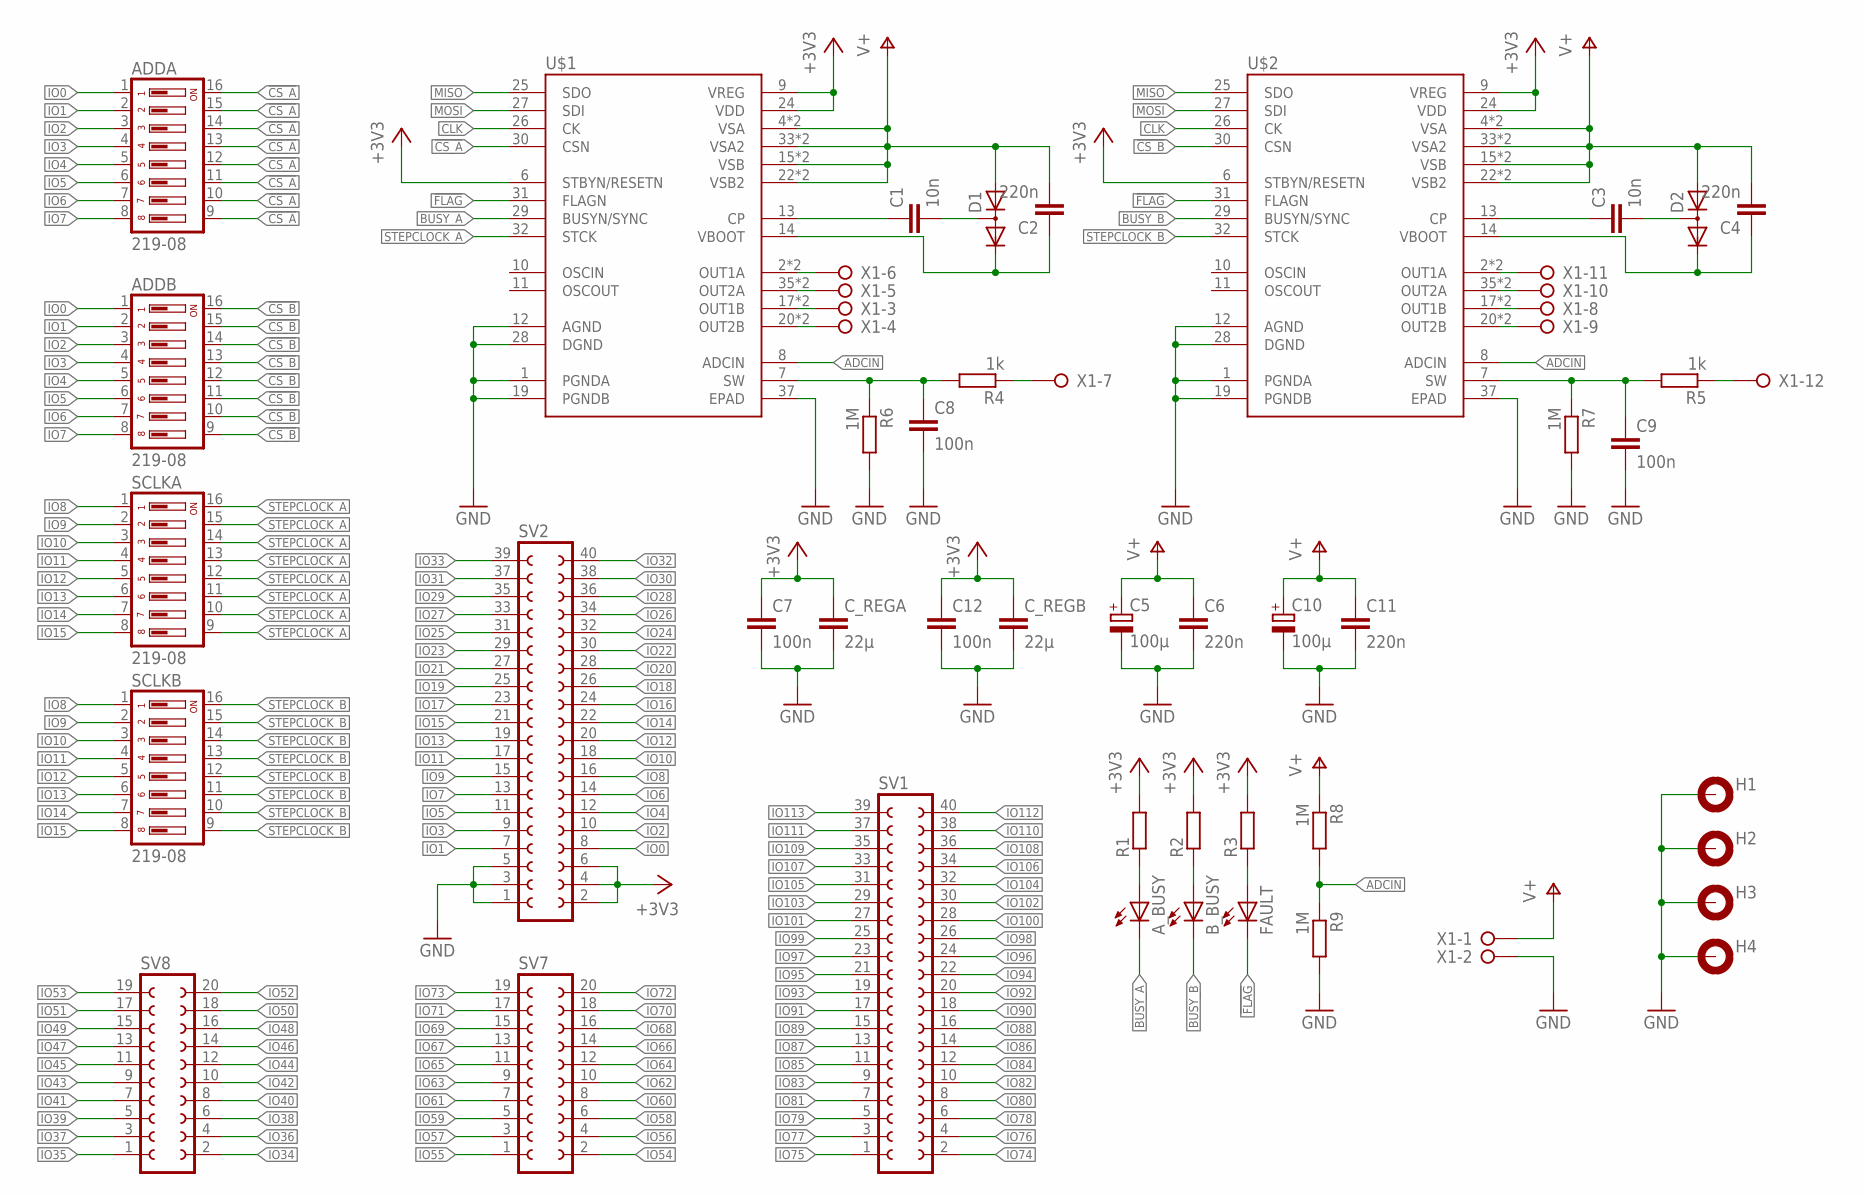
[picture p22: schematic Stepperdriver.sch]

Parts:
ADDA: 219-08; CTS-219-08
ADDB: 219-08; CTS-219-08
A_BUSY: LEDCHIP-LED0805; CHIP-LED0805
B_BUSY: LEDCHIP-LED0805; CHIP-LED0805
C1, C3: 10n; C0805
C2, C4, C6, C11: 220n; C0805
C5, C10: 100µ; 150CLZ-1010
C7, C8, C9, C12: 100n; C0805
C_REGA: 22µ; C0805
C_REGB: 22µ; C0805
D1, D2: DIODE_2CACA-SOT23; SOT23
FAULT: LEDCHIP-LED0805; CHIP-LED0805
H1, H2, H3, H4: MOUNT-PAD-ROUND5.0; 5,0-PAD
R1, R2, R3: R-EU_R0805; R0805
R4, R5: 1k; R0805
R6, R7, R8, R9: 1M; R0805
SCLKA: 219-08; CTS-219-08
SCLKB: 219-08; CTS-219-08
SV1, SV2: FE20-2
SV7, SV8: FE10-2
U$1, U$2: L6470HPOWERSO36; SOP65P1400X360-37N
X1: W237-12P

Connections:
!CS_A: ADDA.9, ADDA.10, ADDA.11, ADDA.12, ADDA.13, ADDA.14, ADDA.15, ADDA.16, U$1.30 (CSN)
!CS_B: ADDB.9, ADDB.10, ADDB.11, ADDB.12, ADDB.13, ADDB.14, ADDB.15, ADDB.16, U$2.30 (CSN)
!FLAG: FAULT.C, U$1.31 (FLAGN), U$2.31 (FLAGN)
+3V3: C7.1, C12.1, C_REGA.1, C_REGB.1, R1.2, R2.2, R3.2, SV2.2, SV2.4, SV2.6, U$1.6 (STBYN/RESETN), U$1.9 (VREG), U$1.24 (VDD), U$2.6 (STBYN/RESETN), U$2.9 (VREG), U$2.24 (VDD)
ADCIN: R8.2, R9.1, U$1.8 (ADCIN), U$2.8 (ADCIN)
BUSY_A: A_BUSY.C, U$1.29 (BUSYN/SYNC)
BUSY_B: B_BUSY.C, U$2.29 (BUSYN/SYNC)
CLK: U$1.26 (CK), U$2.26 (CK)
GND: C5.-, C6.2, C7.2, C8.2, C9.2, C10.-, C11.2, C12.2, C_REGA.2, C_REGB.2, H1.B5, H2.B5, H3.B5, H4.B5, R6.2, R7.2, R9.2, SV2.1, SV2.3, SV2.5, U$1.1 (PGNDA), U$1.12 (AGND), U$1.19 (PGNDB), U$1.28 (DGND), U$1.37 (EPAD), U$2.1 (PGNDA), U$2.12 (AGND), U$2.19 (PGNDB), U$2.28 (DGND), U$2.37 (EPAD), X1.2
IO0: ADDA.1, ADDB.1, SV2.8
IO1: ADDA.2, ADDB.2, SV2.7
IO2: ADDA.3, ADDB.3, SV2.10
IO3: ADDA.4, ADDB.4, SV2.9
IO4: ADDA.5, ADDB.5, SV2.12
IO5: ADDA.6, ADDB.6, SV2.11
IO6: ADDA.7, ADDB.7, SV2.14
IO7: ADDA.8, ADDB.8, SV2.13
IO8: SCLKA.1, SCLKB.1, SV2.16
IO9: SCLKA.2, SCLKB.2, SV2.15
IO10: SCLKA.3, SCLKB.3, SV2.18
IO11: SCLKA.4, SCLKB.4, SV2.17
IO12: SCLKA.5, SCLKB.5, SV2.20
IO13: SCLKA.6, SCLKB.6, SV2.19
IO14: SCLKA.7, SCLKB.7, SV2.22
IO15: SCLKA.8, SCLKB.8, SV2.21
IO16: SV2.24
IO17: SV2.23
IO18: SV2.26
IO19: SV2.25
IO20: SV2.28
IO21: SV2.27
IO22: SV2.30
IO23: SV2.29
IO24: SV2.32
IO25: SV2.31
IO26: SV2.34
IO27: SV2.33
IO28: SV2.36
IO29: SV2.35
IO30: SV2.38
IO31: SV2.37
IO32: SV2.40
IO33: SV2.39
IO34: SV8.2
IO35: SV8.1
IO36: SV8.4
IO37: SV8.3
IO38: SV8.6
IO39: SV8.5
IO40: SV8.8
IO41: SV8.7
IO42: SV8.10
IO43: SV8.9
IO44: SV8.12
IO45: SV8.11
IO46: SV8.14
IO47: SV8.13
IO48: SV8.16
IO49: SV8.15
IO50: SV8.18
IO51: SV8.17
IO52: SV8.20
IO53: SV8.19
IO54: SV7.2
IO55: SV7.1
IO56: SV7.4
IO57: SV7.3
IO58: SV7.6
IO59: SV7.5
IO60: SV7.8
IO61: SV7.7
IO62: SV7.10
IO63: SV7.9
IO64: SV7.12
IO65: SV7.11
IO66: SV7.14
IO67: SV7.13
IO68: SV7.16
IO69: SV7.15
IO70: SV7.18
IO71: SV7.17
IO72: SV7.20
IO73: SV7.19
IO74: SV1.2
IO75: SV1.1
IO76: SV1.4
IO77: SV1.3
IO78: SV1.6
IO79: SV1.5
IO80: SV1.8
IO81: SV1.7
IO82: SV1.10
IO83: SV1.9
IO84: SV1.12
IO85: SV1.11
IO86: SV1.14
IO87: SV1.13
IO88: SV1.16
IO89: SV1.15
IO90: SV1.18
IO91: SV1.17
IO92: SV1.20
IO93: SV1.19
IO94: SV1.22
IO95: SV1.21
IO96: SV1.24
IO97: SV1.23
IO98: SV1.26
IO99: SV1.25
IO100: SV1.28
IO101: SV1.27
IO102: SV1.30
IO103: SV1.29
IO104: SV1.32
IO105: SV1.31
IO106: SV1.34
IO107: SV1.33
IO108: SV1.36
IO109: SV1.35
IO110: SV1.38
IO111: SV1.37
IO112: SV1.40
IO113: SV1.39
MISO: U$1.25 (SDO), U$2.25 (SDO)
MOSI: U$1.27 (SDI), U$2.27 (SDI)
unnamed: U$1.2 (OUT1A), U$1.3 (OUT1A), X1.6
unnamed: U$1.35 (OUT2A), U$1.36 (OUT2A), X1.5
unnamed: U$1.17 (OUT1B), U$1.18 (OUT1B), X1.3
unnamed: U$1.20 (OUT2B), U$1.21 (OUT2B), X1.4
unnamed: U$2.20 (OUT2B), U$2.21 (OUT2B), X1.9
unnamed: U$2.17 (OUT1B), U$2.18 (OUT1B), X1.8
unnamed: U$2.35 (OUT2A), U$2.36 (OUT2A), X1.10
unnamed: U$2.2 (OUT1A), U$2.3 (OUT1A), X1.11
unnamed: C3.1, U$2.13 (CP)
unnamed: C3.2, D2.3 (AC)
unnamed: C4.1, D2.2 (C), U$2.14 (VBOOT)
unnamed: A_BUSY.A, R1.1
unnamed: C1.1, U$1.13 (CP)
unnamed: C1.2, D1.3 (AC)
unnamed: C2.1, D1.2 (C), U$1.14 (VBOOT)
unnamed: R5.1, X1.12
unnamed: B_BUSY.A, R2.1
unnamed: FAULT.A, R3.1
unnamed: C9.1, R5.2, R7.1, U$2.7 (SW)
unnamed: C8.1, R4.2, R6.1, U$1.7 (SW)
unnamed: R4.1, X1.7
STEPCLOCK_A: SCLKA.9, SCLKA.10, SCLKA.11, SCLKA.12, SCLKA.13, SCLKA.14, SCLKA.15, SCLKA.16, U$1.32 (STCK)
STEPCLOCK_B: SCLKB.9, SCLKB.10, SCLKB.11, SCLKB.12, SCLKB.13, SCLKB.14, SCLKB.15, SCLKB.16, U$2.32 (STCK)
V+: C2.2, C4.2, C5.+, C6.1, C10.+, C11.1, D1.1 (A), D2.1 (A), R8.1, U$1.4 (VSA), U$1.5 (VSA), U$1.15 (VSB), U$1.16 (VSB), U$1.22 (VSB2), U$1.23 (VSB2), U$1.33 (VSA2), U$1.34 (VSA2), U$2.4 (VSA), U$2.5 (VSA), U$2.15 (VSB), U$2.16 (VSB), U$2.22 (VSB2), U$2.23 (VSB2), U$2.33 (VSA2), U$2.34 (VSA2), X1.1

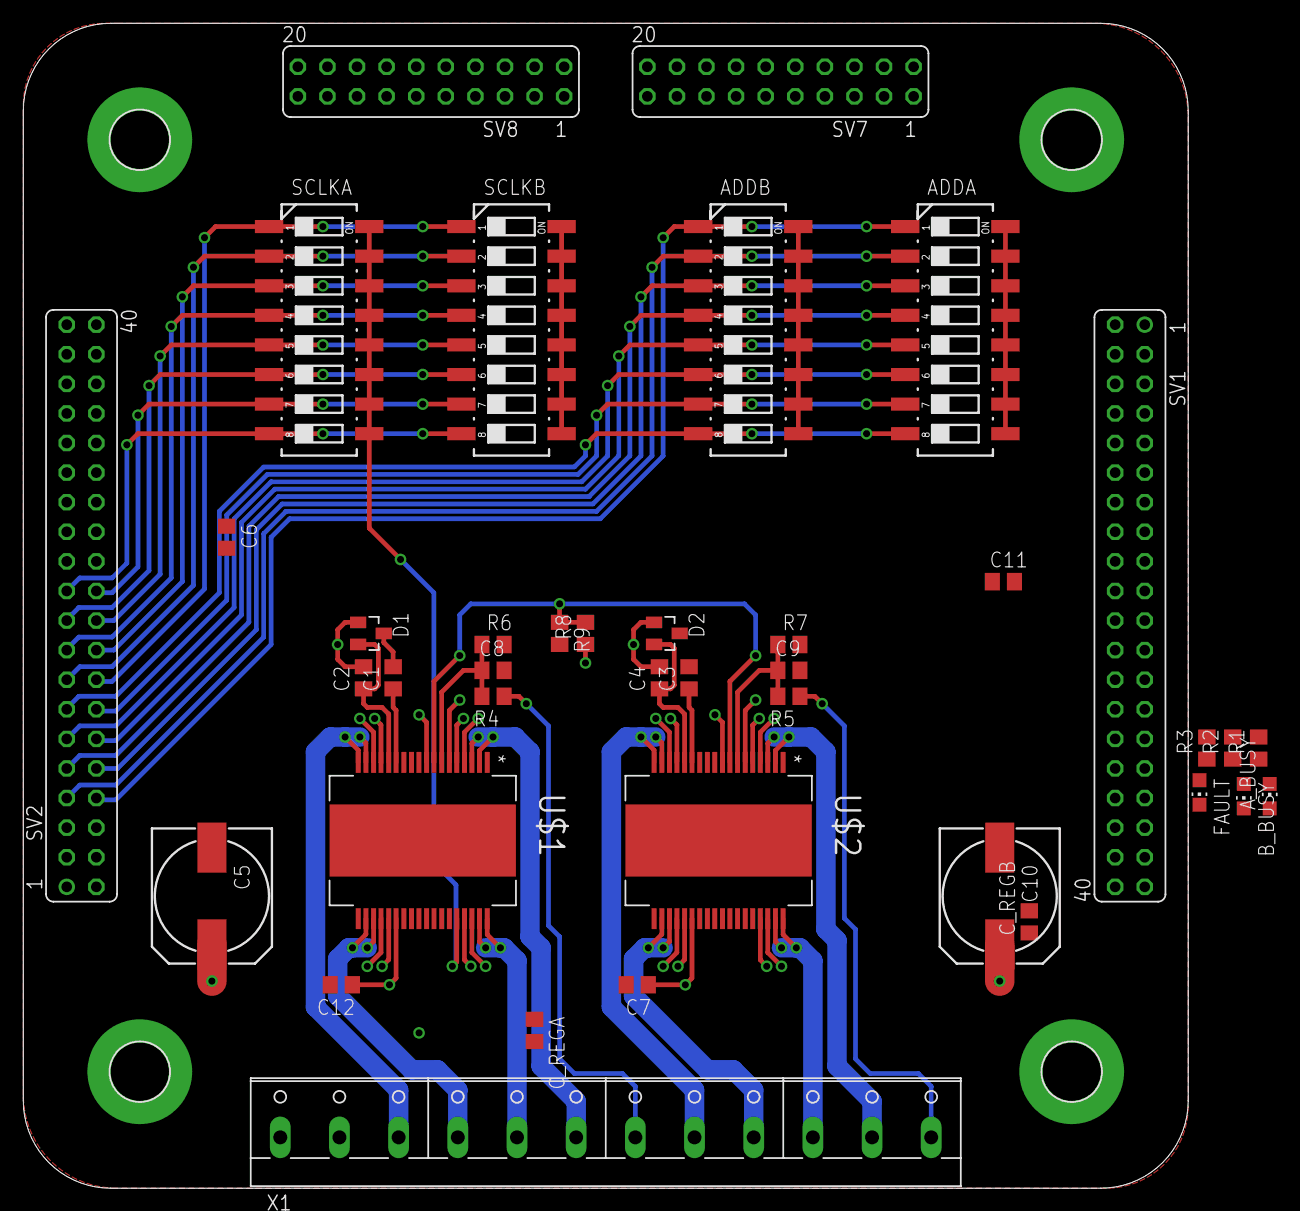
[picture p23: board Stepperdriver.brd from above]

Board: 4 copper layers, 100.0 x 100.0 mm, 43 parts (0 on the bottom side), 51 nets.

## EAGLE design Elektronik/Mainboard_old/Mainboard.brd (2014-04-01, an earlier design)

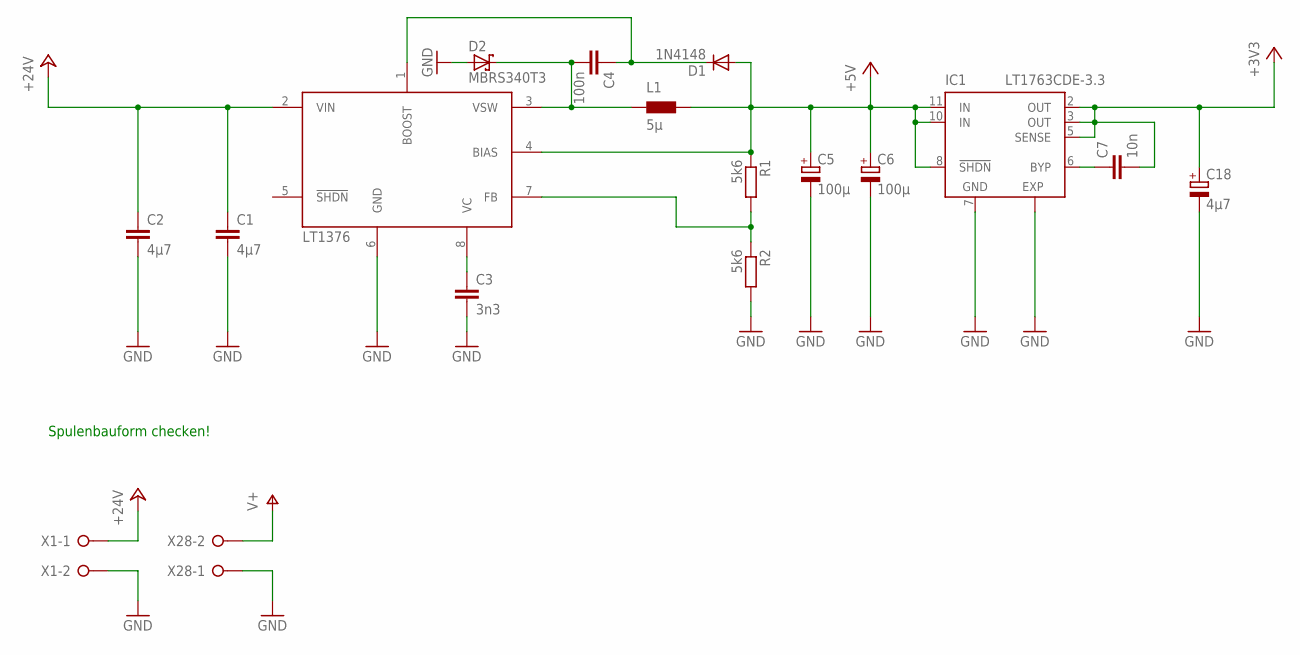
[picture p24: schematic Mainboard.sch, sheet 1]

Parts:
C1, C2: 4µ7; C0805
C3: 3n3; C0805
C4: 100n; C0805
C5, C6: 100µ; UD-6,3X7,7_NICHICON
C7: 10n; C0805
C18: 4µ7; UD-6,3X7,7_NICHICON
D1: 1N4148; SOD123
D2: MBRS340T3; SMC
IC1: LT1763CDE-3.3; DFN12
L1: 5µ; PIS4720
R1, R2: 5k6; R0805
U$1: LT1376; SOIC8
X1, X28: W237-02P; W237-132

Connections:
+3V3: C7.2, C18.+, IC1.2 (OUT), IC1.3 (OUT), IC1.5 (SENSE); also elsewhere on the board
+5V: C5.+, C6.+, D1.A, IC1.8 (!SHDN), IC1.10 (IN), IC1.11 (IN), L1.P$2, R1.1, U$1.4 (BIAS)
+24V: C1.1, C2.1, U$1.2 (VIN), X1.1
GND: C1.2, C2.2, C3.2, C5.-, C6.-, C18.-, D2.A, IC1.7 (GND), IC1.EXP, R2.2, U$1.6 (GND), X1.2, X28.1; also elsewhere on the board
unnamed: C3.1, U$1.8 (VC)
unnamed: C4.2, D2.C, L1.P$1, U$1.3 (VSW)
unnamed: C4.1, D1.C, U$1.1 (BOOST)
unnamed: R1.2, R2.1, U$1.7 (FB)
unnamed: C7.1, IC1.6 (BYP)
V+: X28.2; also elsewhere on the board

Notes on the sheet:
Spulenbauform checken!

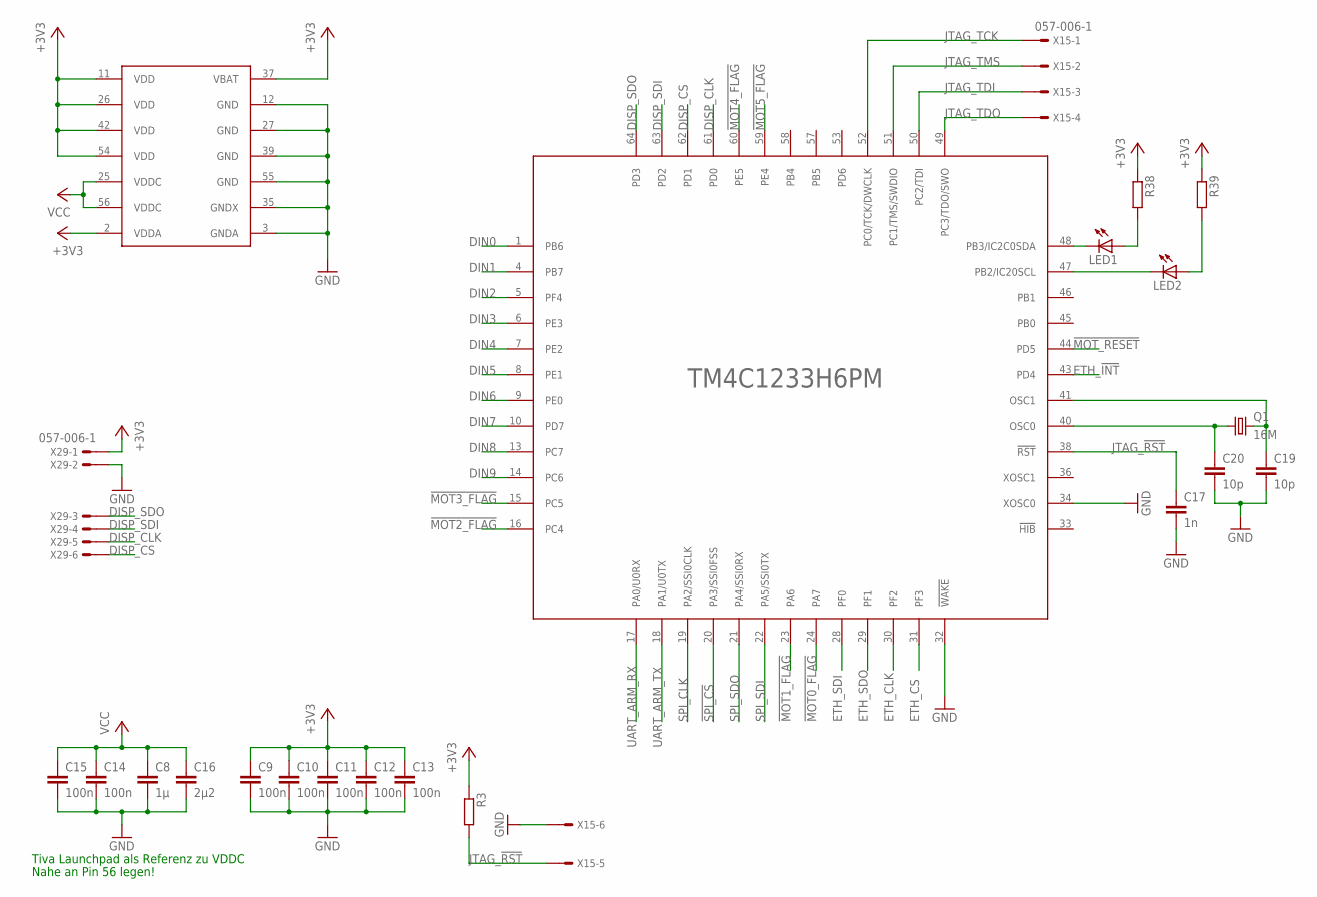
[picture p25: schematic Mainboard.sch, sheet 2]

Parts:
C8: 1µ; C0805
C9, C10, C11, C12, C13, C14, C15: 100n; C0805
C16: 2µ2; C0805
C17: 1n; C0805
C19, C20: 10p; C0805
LED1, LED2: LEDSML0805; SML0805
Q1: 16M; SM49
R3, R38, R39: R-EU_R0805; R0805
U$2: TM4C1233H6PM; QFP50P1200X1200X160-64N
X15, X29: 057-006-1

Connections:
!MOT0_FLAG: U$2.24 (PA7); also elsewhere on the board
!MOT1_FLAG: U$2.23 (PA6); also elsewhere on the board
!MOT2_FLAG: U$2.16 (PC4); also elsewhere on the board
!MOT3_FLAG: U$2.15 (PC5); also elsewhere on the board
!MOT4_FLAG: U$2.60 (PE5); also elsewhere on the board
!MOT5_FLAG: U$2.59 (PE4); also elsewhere on the board
!MOT_RESET: U$2.44 (PD5); also elsewhere on the board
!SPI_CS: U$2.20 (PA3/SSI0FSS); also elsewhere on the board
+3V3: C9.1, C10.1, C11.1, C12.1, C13.1, R3.1, R38.1, R39.1, U$2.2 (VDDA), U$2.11 (VDD), U$2.26 (VDD), U$2.37 (VBAT), U$2.42 (VDD), U$2.54 (VDD), X29.1; also elsewhere on the board
DIN0: U$2.1 (PB6); also elsewhere on the board
DIN1: U$2.4 (PB7); also elsewhere on the board
DIN2: U$2.5 (PF4); also elsewhere on the board
DIN3: U$2.6 (PE3); also elsewhere on the board
DIN4: U$2.7 (PE2); also elsewhere on the board
DIN5: U$2.8 (PE1); also elsewhere on the board
DIN6: U$2.9 (PE0); also elsewhere on the board
DIN7: U$2.10 (PD7); also elsewhere on the board
DIN8: U$2.13 (PC7); also elsewhere on the board
DIN9: U$2.14 (PC6); also elsewhere on the board
DISP_CLK: U$2.61 (PD0), X29.5
DISP_CS: U$2.62 (PD1), X29.6
DISP_SDI: U$2.63 (PD2), X29.4
DISP_SDO: U$2.64 (PD3), X29.3
ETH_!INT: U$2.43 (PD4); also elsewhere on the board
ETH_CLK: U$2.30 (PF2); also elsewhere on the board
ETH_CS: U$2.31 (PF3); also elsewhere on the board
ETH_SDI: U$2.28 (PF0); also elsewhere on the board
ETH_SDO: U$2.29 (PF1); also elsewhere on the board
GND: C8.2, C9.2, C10.2, C11.2, C12.2, C13.2, C14.2, C15.2, C16.2, C17.2, C19.2, C20.2, U$2.3 (GNDA), U$2.12 (GND), U$2.27 (GND), U$2.32 (!WAKE), U$2.34 (XOSC0), U$2.35 (GNDX), U$2.39 (GND), U$2.55 (GND), X15.6, X29.2; also elsewhere on the board
JTAG_!RST: C17.1, R3.2, U$2.38 (!RST), X15.5
JTAG_TCK: U$2.52 (PC0/TCK/DWCLK), X15.1
JTAG_TDI: U$2.50 (PC2/TDI), X15.3
JTAG_TDO: U$2.49 (PC3/TDO/SWO), X15.4
JTAG_TMS: U$2.51 (PC1/TMS/SWDIO), X15.2
unnamed: LED1.C, U$2.48 (PB3/IC2C0SDA)
unnamed: C19.1, Q1.2, U$2.41 (OSC1)
unnamed: C20.1, Q1.1, U$2.40 (OSC0)
unnamed: LED1.A, R38.2
unnamed: LED2.A, R39.2
unnamed: LED2.C, U$2.47 (PB2/IC20SCL)
SPI_CLK: U$2.19 (PA2/SSI0CLK); also elsewhere on the board
SPI_SDI: U$2.22 (PA5/SSI0TX); also elsewhere on the board
SPI_SDO: U$2.21 (PA4/SSI0RX); also elsewhere on the board
UART_ARM_RX: U$2.17 (PA0/U0RX); also elsewhere on the board
UART_ARM_TX: U$2.18 (PA1/U0TX); also elsewhere on the board
VCC: C8.1, C14.1, C15.1, C16.1, U$2.25 (VDDC), U$2.56 (VDDC)

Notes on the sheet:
Tiva Launchpad als Referenz zu VDDC
Nahe an Pin 56 legen!

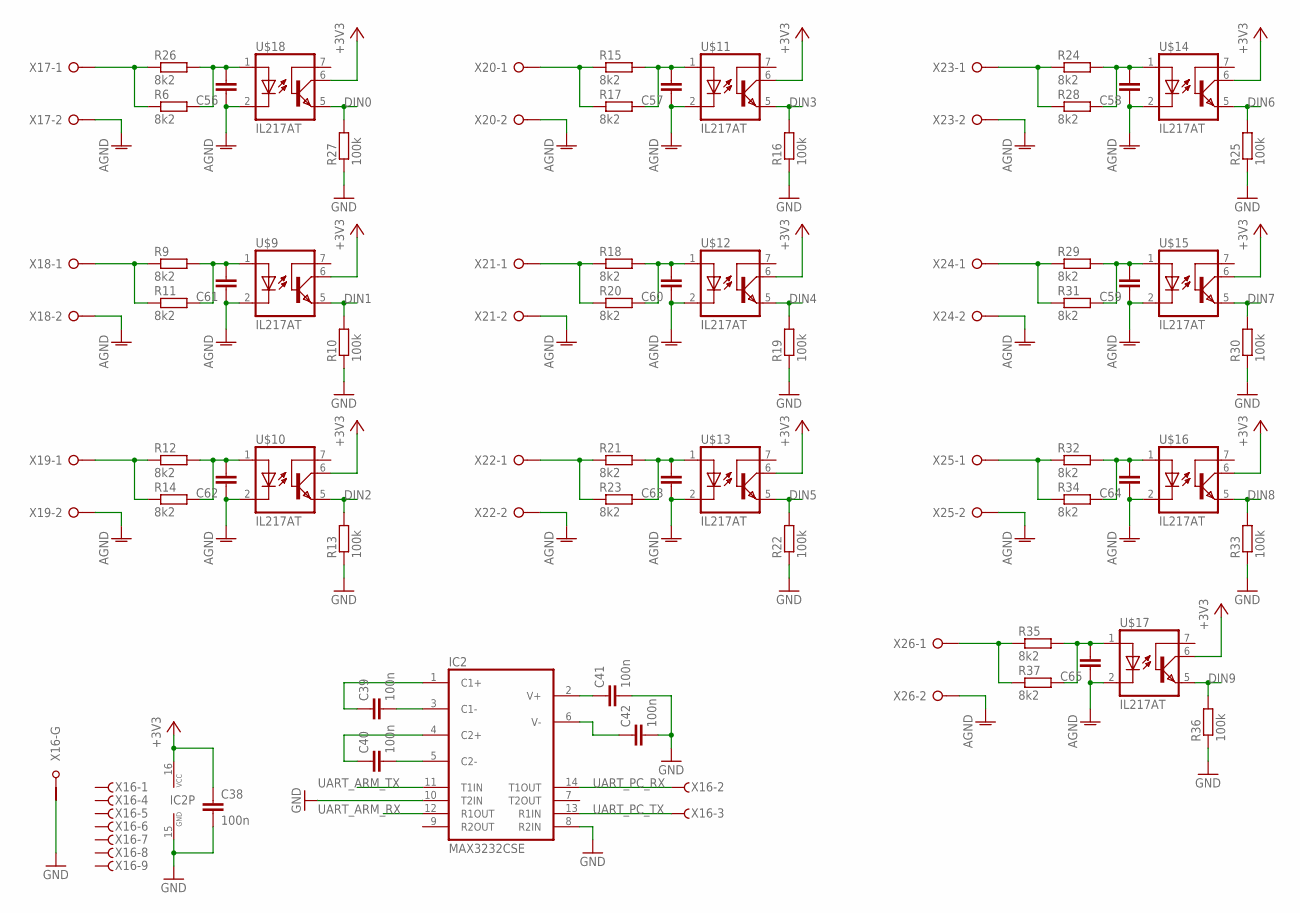
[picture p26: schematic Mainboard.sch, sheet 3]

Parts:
C38, C39, C40, C41, C42: 100n; C0805
C56, C57, C58, C59, C60, C61, C62, C63, C64, C65: C-EUC1210; C1210
IC2: MAX3232CSE; SO16
R6, R9, R11, R12, R14, R15, R17, R18, R20, R21, R23, R24, R26, R28, R29, R31, R32, R34, R35, R37: 8k2; R0805
R10, R13, R16, R19, R22, R25, R27, R30, R33, R36: 100k; R0805
U$9, U$10, U$11, U$12, U$13, U$14, U$15, U$16, U$17, U$18: IL217AT; SOIC8
X16: F09HPS; F09HP
X17, X18, X19, X20, X21, X22, X23, X24, X25, X26: W237-02P; W237-132

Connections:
+3V3: C38.1, IC2.16 (VCC), U$9.6 (COL), U$10.6 (COL), U$11.6 (COL), U$12.6 (COL), U$13.6 (COL), U$14.6 (COL), U$15.6 (COL), U$16.6 (COL), U$17.6 (COL), U$18.6 (COL); also elsewhere on the board
DIN0: R27.2, U$18.5 (EMI); also elsewhere on the board
DIN1: R10.2, U$9.5 (EMI); also elsewhere on the board
DIN2: R13.2, U$10.5 (EMI); also elsewhere on the board
DIN3: R16.2, U$11.5 (EMI); also elsewhere on the board
DIN4: R19.2, U$12.5 (EMI); also elsewhere on the board
DIN5: R22.2, U$13.5 (EMI); also elsewhere on the board
DIN6: R25.2, U$14.5 (EMI); also elsewhere on the board
DIN7: R30.2, U$15.5 (EMI); also elsewhere on the board
DIN8: R33.2, U$16.5 (EMI); also elsewhere on the board
DIN9: R36.2, U$17.5 (EMI); also elsewhere on the board
GND: C38.2, C41.2, C42.2, IC2.8 (R2IN), IC2.10 (T2IN), IC2.15 (GND), R10.1, R13.1, R16.1, R19.1, R22.1, R25.1, R27.1, R30.1, R33.1, R36.1, X16.G1; also elsewhere on the board
IGND: C56.1, C57.1, C58.1, C59.1, C60.1, C61.1, C62.1, C63.1, C64.1, C65.1, U$9.2 (C), U$10.2 (C), U$11.2 (C), U$12.2 (C), U$13.2 (C), U$14.2 (C), U$15.2 (C), U$16.2 (C), U$17.2 (C), U$18.2 (C), X17.2, X18.2, X19.2, X20.2, X21.2, X22.2, X23.2, X24.2, X25.2, X26.2
unnamed: C40.1, IC2.4 (C2+)
unnamed: C39.2, IC2.3 (C1-)
unnamed: C42.1, IC2.6 (V-)
unnamed: C41.1, IC2.2 (V+)
unnamed: C40.2, IC2.5 (C2-)
unnamed: C39.1, IC2.1 (C1+)
unnamed: C56.2, R6.2, R26.2, U$18.1 (A)
unnamed: R6.1, R26.1, X17.1
unnamed: R9.1, R11.1, X18.1
unnamed: C61.2, R9.2, R11.2, U$9.1 (A)
unnamed: R12.1, R14.1, X19.1
unnamed: C62.2, R12.2, R14.2, U$10.1 (A)
unnamed: R15.1, R17.1, X20.1
unnamed: C57.2, R15.2, R17.2, U$11.1 (A)
unnamed: R18.1, R20.1, X21.1
unnamed: C60.2, R18.2, R20.2, U$12.1 (A)
unnamed: R21.1, R23.1, X22.1
unnamed: C63.2, R21.2, R23.2, U$13.1 (A)
unnamed: R24.1, R28.1, X23.1
unnamed: C58.2, R24.2, R28.2, U$14.1 (A)
unnamed: R29.1, R31.1, X24.1
unnamed: C59.2, R29.2, R31.2, U$15.1 (A)
unnamed: R32.1, R34.1, X25.1
unnamed: C64.2, R32.2, R34.2, U$16.1 (A)
unnamed: R35.1, R37.1, X26.1
unnamed: C65.2, R35.2, R37.2, U$17.1 (A)
UART_ARM_RX: IC2.12 (R1OUT); also elsewhere on the board
UART_ARM_TX: IC2.11 (T1IN); also elsewhere on the board
UART_PC_RX: IC2.14 (T1OUT), X16.2 (F)
UART_PC_TX: IC2.13 (R1IN), X16.3 (F)

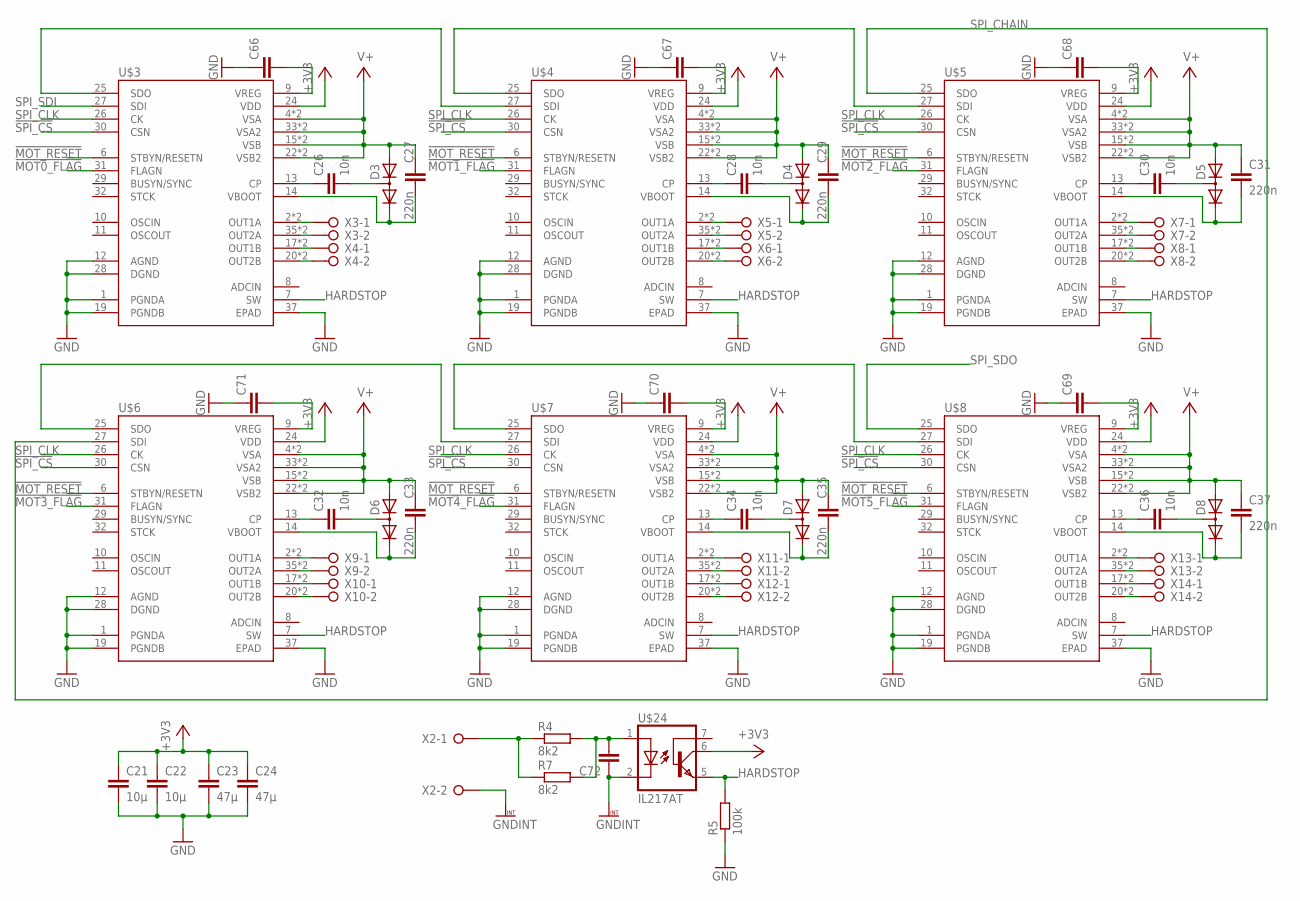
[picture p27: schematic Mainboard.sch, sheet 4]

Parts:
C21, C22: 10µ; C0805
C23, C24: 47µ; C0805
C26, C28, C30, C32, C34, C36: 10n; C0805
C27, C29, C31, C33, C35, C37: 220n; C0805
C66, C67, C68, C69, C70, C71, C72: C-EUC1210; C1210
D3, D4, D5, D6, D7, D8: HSMS-2802-TR1G; SOT23
R4, R7: 8k2; R0805
R5: 100k; R0805
U$3, U$4, U$5, U$6, U$7, U$8: L6470HPOWERSO36; SOP65P1400X360-37N
U$24: IL217AT; SOIC8
X2, X3, X4, X5, X6, X7, X8, X9, X10, X11, X12, X13, X14: W237-02P; W237-132

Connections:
!MOT0_FLAG: U$3.31 (FLAGN); also elsewhere on the board
!MOT1_FLAG: U$4.31 (FLAGN); also elsewhere on the board
!MOT2_FLAG: U$5.31 (FLAGN); also elsewhere on the board
!MOT3_FLAG: U$6.31 (FLAGN); also elsewhere on the board
!MOT4_FLAG: U$7.31 (FLAGN); also elsewhere on the board
!MOT5_FLAG: U$8.31 (FLAGN); also elsewhere on the board
!MOT_RESET: U$3.6 (STBYN/RESETN), U$4.6 (STBYN/RESETN), U$5.6 (STBYN/RESETN), U$6.6 (STBYN/RESETN), U$7.6 (STBYN/RESETN), U$8.6 (STBYN/RESETN); also elsewhere on the board
!SPI_CS: U$3.30 (CSN), U$4.30 (CSN), U$5.30 (CSN), U$6.30 (CSN), U$7.30 (CSN), U$8.30 (CSN); also elsewhere on the board
+3V3: C21.1, C22.1, C23.1, C24.1, U$3.24 (VDD), U$4.24 (VDD), U$5.24 (VDD), U$6.24 (VDD), U$7.24 (VDD), U$8.24 (VDD), U$24.6 (COL); also elsewhere on the board
GND: C21.2, C22.2, C23.2, C24.2, C66.1, C67.1, C68.1, C69.1, C70.1, C71.1, R5.1, U$3.1 (PGNDA), U$3.12 (AGND), U$3.19 (PGNDB), U$3.28 (DGND), U$3.37 (EPAD), U$4.1 (PGNDA), U$4.12 (AGND), U$4.19 (PGNDB), U$4.28 (DGND), U$4.37 (EPAD), U$5.1 (PGNDA), U$5.12 (AGND), U$5.19 (PGNDB), U$5.28 (DGND), U$5.37 (EPAD), U$6.1 (PGNDA), U$6.12 (AGND), U$6.19 (PGNDB), U$6.28 (DGND), U$6.37 (EPAD), U$7.1 (PGNDA), U$7.12 (AGND), U$7.19 (PGNDB), U$7.28 (DGND), U$7.37 (EPAD), U$8.1 (PGNDA), U$8.12 (AGND), U$8.19 (PGNDB), U$8.28 (DGND), U$8.37 (EPAD); also elsewhere on the board
GND@5: R4.1, R7.1, X2.1
GNDINT: C72.1, U$24.2 (C), X2.2
HARDSTOP: R5.2, U$3.7 (SW), U$4.7 (SW), U$5.7 (SW), U$6.7 (SW), U$7.7 (SW), U$8.7 (SW), U$24.5 (EMI)
unnamed: U$3.25 (SDO), U$4.27 (SDI)
unnamed: U$6.25 (SDO), U$7.27 (SDI)
unnamed: C26.1, U$3.13 (CP)
unnamed: C27.2, D3.2 (C), U$3.14 (VBOOT)
unnamed: C26.2, D3.3 (AC)
unnamed: C28.1, U$4.13 (CP)
unnamed: C29.2, D4.2 (C), U$4.14 (VBOOT)
unnamed: U$4.25 (SDO), U$5.27 (SDI)
unnamed: C28.2, D4.3 (AC)
unnamed: U$3.2 (OUT1A), U$3.3 (OUT1A), X3.1
unnamed: U$3.35 (OUT2A), U$3.36 (OUT2A), X3.2
unnamed: U$3.17 (OUT1B), U$3.18 (OUT1B), X4.1
unnamed: U$3.20 (OUT2B), U$3.21 (OUT2B), X4.2
unnamed: U$4.2 (OUT1A), U$4.3 (OUT1A), X5.1
unnamed: U$4.35 (OUT2A), U$4.36 (OUT2A), X5.2
unnamed: U$4.17 (OUT1B), U$4.18 (OUT1B), X6.1
unnamed: U$4.20 (OUT2B), U$4.21 (OUT2B), X6.2
unnamed: C31.2, D5.2 (C), U$5.14 (VBOOT)
unnamed: C30.2, D5.3 (AC)
unnamed: C30.1, U$5.13 (CP)
unnamed: U$5.2 (OUT1A), U$5.3 (OUT1A), X7.1
unnamed: U$5.35 (OUT2A), U$5.36 (OUT2A), X7.2
unnamed: U$5.17 (OUT1B), U$5.18 (OUT1B), X8.1
unnamed: U$5.20 (OUT2B), U$5.21 (OUT2B), X8.2
unnamed: U$7.25 (SDO), U$8.27 (SDI)
unnamed: C32.1, U$6.13 (CP)
unnamed: C33.2, D6.2 (C), U$6.14 (VBOOT)
unnamed: C32.2, D6.3 (AC)
unnamed: C35.2, D7.2 (C), U$7.14 (VBOOT)
unnamed: C34.2, D7.3 (AC)
unnamed: C34.1, U$7.13 (CP)
unnamed: U$6.2 (OUT1A), U$6.3 (OUT1A), X9.1
unnamed: U$6.35 (OUT2A), U$6.36 (OUT2A), X9.2
unnamed: U$6.17 (OUT1B), U$6.18 (OUT1B), X10.1
unnamed: U$6.20 (OUT2B), U$6.21 (OUT2B), X10.2
unnamed: U$7.2 (OUT1A), U$7.3 (OUT1A), X11.1
unnamed: U$7.35 (OUT2A), U$7.36 (OUT2A), X11.2
unnamed: U$7.17 (OUT1B), U$7.18 (OUT1B), X12.1
unnamed: U$7.20 (OUT2B), U$7.21 (OUT2B), X12.2
unnamed: C37.2, D8.2 (C), U$8.14 (VBOOT)
unnamed: C36.2, D8.3 (AC)
unnamed: C36.1, U$8.13 (CP)
unnamed: U$8.2 (OUT1A), U$8.3 (OUT1A), X13.1
unnamed: U$8.35 (OUT2A), U$8.36 (OUT2A), X13.2
unnamed: U$8.17 (OUT1B), U$8.18 (OUT1B), X14.1
unnamed: U$8.20 (OUT2B), U$8.21 (OUT2B), X14.2
unnamed: C66.2, U$3.9 (VREG)
unnamed: C67.2, U$4.9 (VREG)
unnamed: C68.2, U$5.9 (VREG)
unnamed: C69.2, U$8.9 (VREG)
unnamed: C70.2, U$7.9 (VREG)
unnamed: C71.2, U$6.9 (VREG)
unnamed: C72.2, R4.2, R7.2, U$24.1 (A)
SPI_CHAIN: U$5.25 (SDO), U$6.27 (SDI)
SPI_CLK: U$3.26 (CK), U$4.26 (CK), U$5.26 (CK), U$6.26 (CK), U$7.26 (CK), U$8.26 (CK); also elsewhere on the board
SPI_SDI: U$3.27 (SDI); also elsewhere on the board
SPI_SDO: U$8.25 (SDO); also elsewhere on the board
V+: C27.1, C29.1, C31.1, C33.1, C35.1, C37.1, D3.1 (A), D4.1 (A), D5.1 (A), D6.1 (A), D7.1 (A), D8.1 (A), U$3.4 (VSA), U$3.5 (VSA), U$3.15 (VSB), U$3.16 (VSB), U$3.22 (VSB2), U$3.23 (VSB2), U$3.33 (VSA2), U$3.34 (VSA2), U$4.4 (VSA), U$4.5 (VSA), U$4.15 (VSB), U$4.16 (VSB), U$4.22 (VSB2), U$4.23 (VSB2), U$4.33 (VSA2), U$4.34 (VSA2), U$5.4 (VSA), U$5.5 (VSA), U$5.15 (VSB), U$5.16 (VSB), U$5.22 (VSB2), U$5.23 (VSB2), U$5.33 (VSA2), U$5.34 (VSA2), U$6.4 (VSA), U$6.5 (VSA), U$6.15 (VSB), U$6.16 (VSB), U$6.22 (VSB2), U$6.23 (VSB2), U$6.33 (VSA2), U$6.34 (VSA2), U$7.4 (VSA), U$7.5 (VSA), U$7.15 (VSB), U$7.16 (VSB), U$7.22 (VSB2), U$7.23 (VSB2), U$7.33 (VSA2), U$7.34 (VSA2), U$8.4 (VSA), U$8.5 (VSA), U$8.15 (VSB), U$8.16 (VSB), U$8.22 (VSB2), U$8.23 (VSB2), U$8.33 (VSA2), U$8.34 (VSA2); also elsewhere on the board

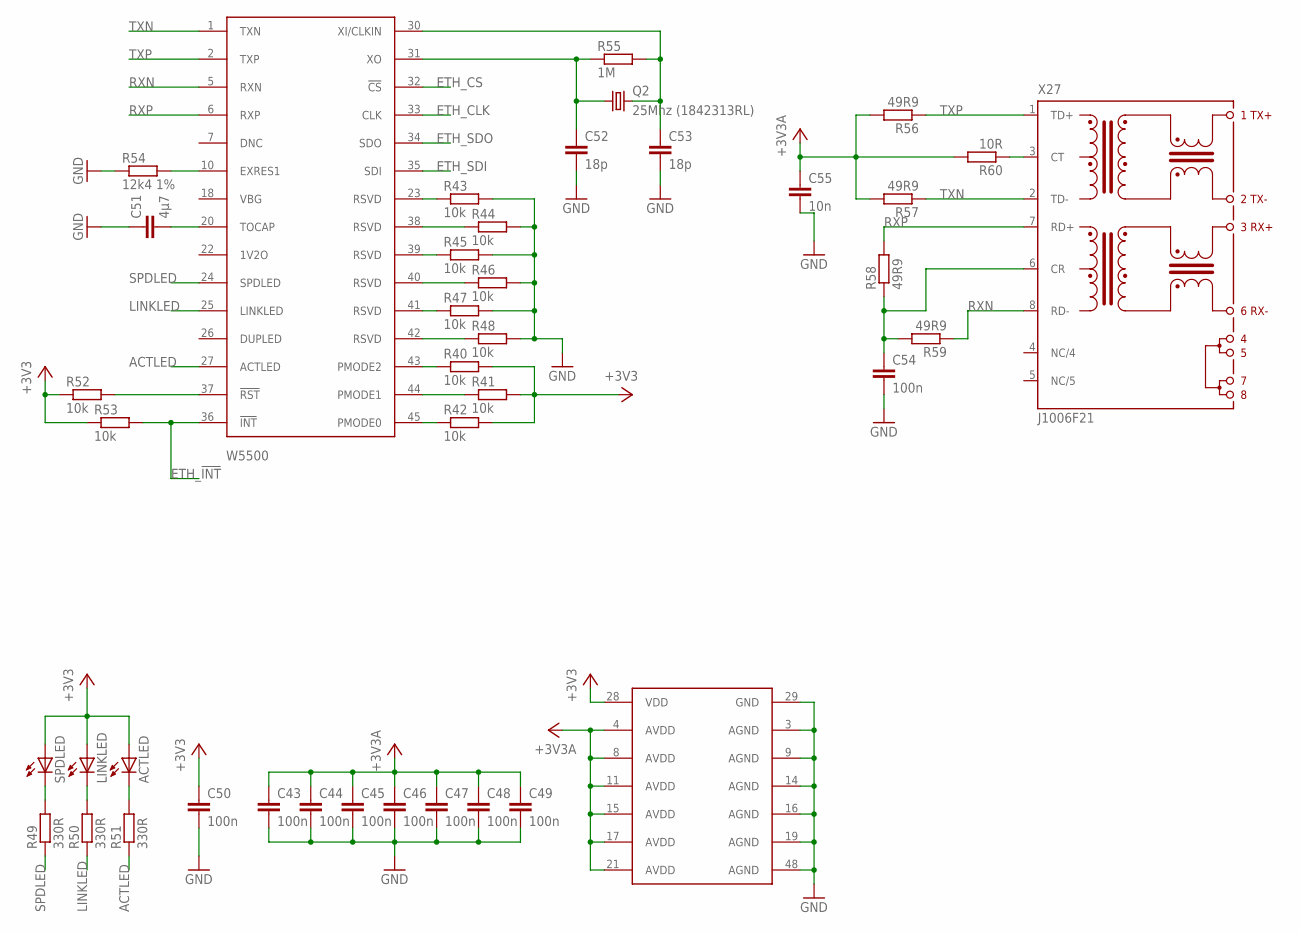
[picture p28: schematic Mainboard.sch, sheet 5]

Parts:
ACTLED: LEDCHIPLED_0805; CHIPLED_0805
C43, C44, C45, C46, C47, C48, C49, C50, C54: 100n; C0805
C51: 4µ7; C0805
C52, C53: 18p; C0805
C55: 10n; C0805
LINKLED: LEDCHIPLED_0805; CHIPLED_0805
Q2: 25Mhz (1842313RL); HC49UP
R40, R41, R42, R43, R44, R45, R46, R47, R48, R52, R53: 10k; R0805
R49, R50, R51: 330R; R0805
R54: 12k4 1%; R0805
R55: 1M; R0805
R56, R57, R58, R59: 49R9; R0805
R60: 10R; R0805
SPDLED: LEDCHIPLED_0805; CHIPLED_0805
U$19: W5500; LQFP48
X27: J1006F21; J1

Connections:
+3V3: ACTLED.A, C43.1, C44.1, C45.1, C46.1, C47.1, C48.1, C49.1, C50.1, C55.1, LINKLED.A, R40.2, R41.2, R42.2, R52.1, R53.1, R56.2, R57.2, R60.2, SPDLED.A, U$19.4 (AVDD), U$19.8 (AVDD), U$19.11 (AVDD), U$19.15 (AVDD), U$19.17 (AVDD), U$19.21 (AVDD), U$19.28 (VDD); also elsewhere on the board
ACTLED: R51.1, U$19.27 (ACTLED)
ETH_!INT: R53.2, U$19.36 (!INT); also elsewhere on the board
ETH_CLK: U$19.33 (CLK); also elsewhere on the board
ETH_CS: U$19.32 (!CS); also elsewhere on the board
ETH_SDI: U$19.35 (SDI); also elsewhere on the board
ETH_SDO: U$19.34 (SDO); also elsewhere on the board
GND: C43.2, C44.2, C45.2, C46.2, C47.2, C48.2, C49.2, C50.2, C51.1, C52.2, C53.2, C54.2, C55.2, R43.2, R44.2, R45.2, R46.2, R47.2, R48.2, R54.1, U$19.3 (AGND), U$19.9 (AGND), U$19.14 (AGND), U$19.16 (AGND), U$19.19 (AGND), U$19.29 (GND), U$19.48 (AGND); also elsewhere on the board
LINKLED: R50.1, U$19.25 (LINKLED)
unnamed: R43.1, U$19.23 (RSVD)
unnamed: R44.1, U$19.38 (RSVD)
unnamed: R45.1, U$19.39 (RSVD)
unnamed: R46.1, U$19.40 (RSVD)
unnamed: R40.1, U$19.43 (PMODE2)
unnamed: R41.1, U$19.44 (PMODE1)
unnamed: R42.1, U$19.45 (PMODE0)
unnamed: R47.1, U$19.41 (RSVD)
unnamed: R48.1, U$19.42 (RSVD)
unnamed: R52.2, U$19.37 (!RST)
unnamed: R49.2, SPDLED.C
unnamed: LINKLED.C, R50.2
unnamed: ACTLED.C, R51.2
unnamed: R54.2, U$19.10 (EXRES1)
unnamed: C51.2, U$19.20 (TOCAP)
unnamed: C53.1, Q2.2, R55.2, U$19.30 (XI/CLKIN)
unnamed: C52.1, Q2.1, R55.1, U$19.31 (XO)
unnamed: C54.1, R58.1, R59.2, X27.6 (CR)
unnamed: R60.1, X27.3 (CT)
RXN: R59.1, U$19.5 (RXN), X27.8 (RD-)
RXP: R58.2, U$19.6 (RXP), X27.7 (RD+)
SPDLED: R49.1, U$19.24 (SPDLED)
TXN: R57.1, U$19.1 (TXN), X27.2 (TD-)
TXP: R56.1, U$19.2 (TXP), X27.1 (TD+)

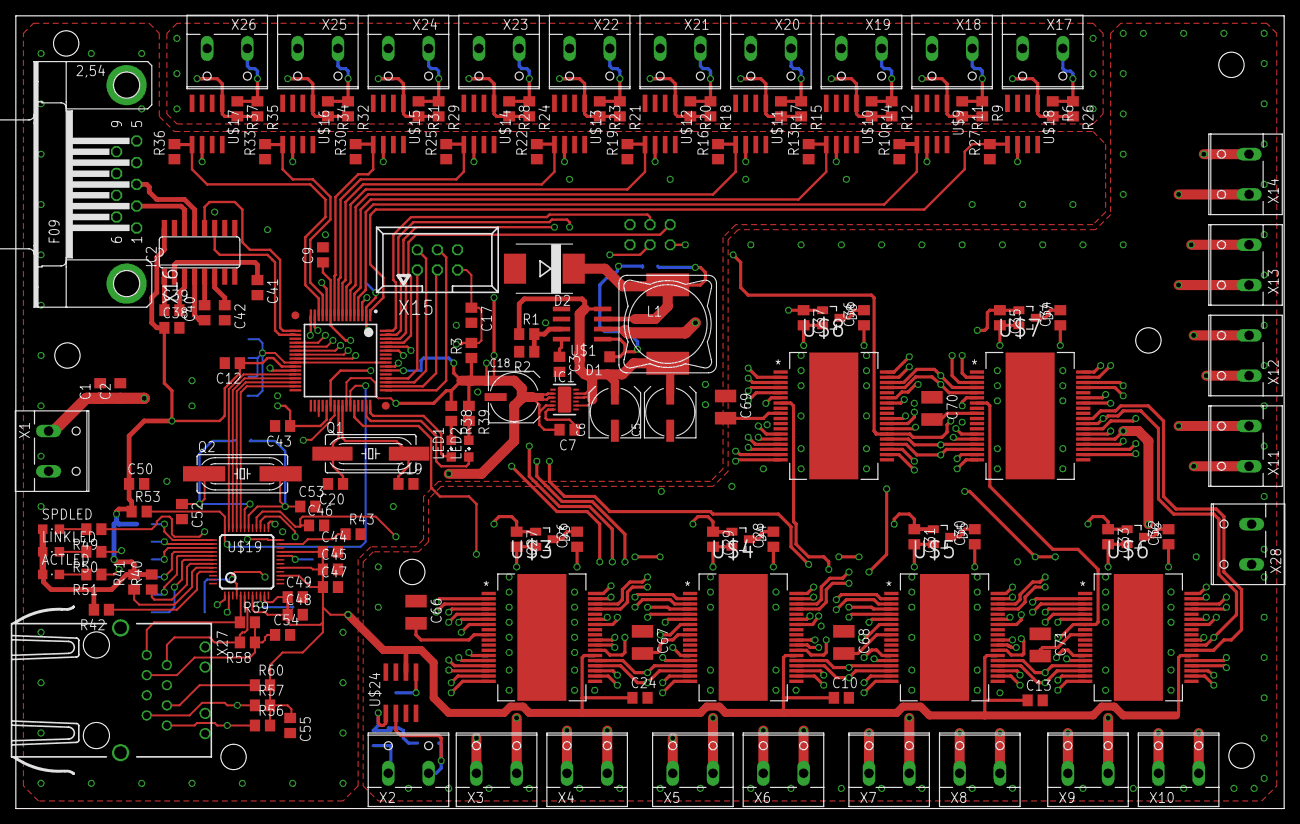
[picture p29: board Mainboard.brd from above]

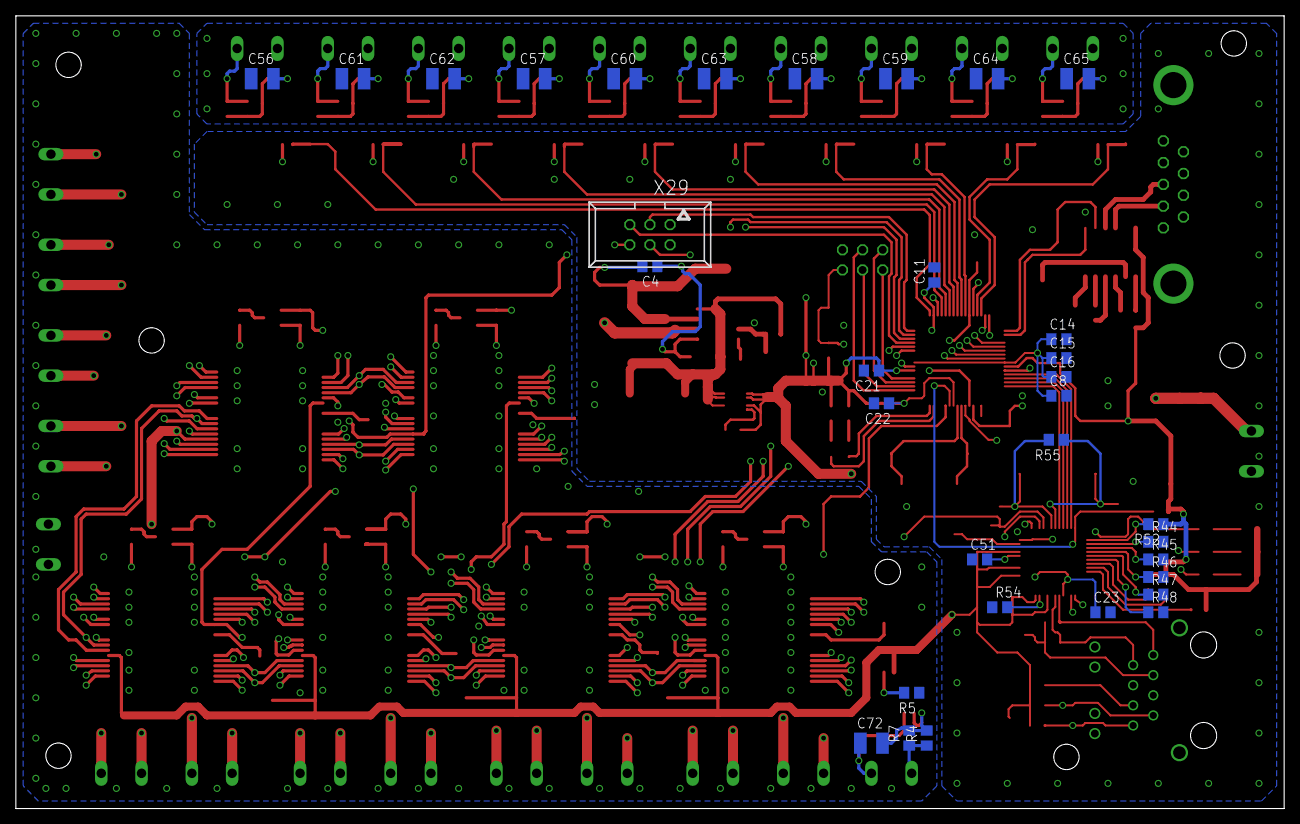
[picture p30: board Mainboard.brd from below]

Board: 4 copper layers, 160.0 x 100.0 mm, 197 parts (33 on the bottom side), 166 nets.

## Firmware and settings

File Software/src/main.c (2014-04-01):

/*
 * main.c
 *
 *  Created on: 19.10.2013
 *      Author: einball
 */
#if 1 // ausblenden der #include befehle, zum verbessern des "workflows"
#define TARGET_IS_BLIZZARD_RA2
#define TM4C123GH6PM
#include <stdint.h>
#include <stdlib.h>
#include <stdbool.h>

#include <driverlib/interrupt.h>
#include <driverlib/sysctl.h>
#include <driverlib/uart.h>
#include <driverlib/ssi.h>
#include <driverlib/gpio.h>
#include <driverlib/watchdog.h>
#include <driverlib/timer.h>
#include <driverlib/rom.h>
#include <driverlib/rom_map.h>

#include <hardware/hw_nvic.h>
#include <hardware/hw_ints.h>
#include <hardware/hw_sysctl.h>
#include <hardware/hw_uart.h>
#include <hardware/hw_ssi.h>
#include <hardware/hw_gpio.h>
#include <hardware/hw_watchdog.h>
#include <hardware/hw_timer.h>
#include <hardware/hw_memmap.h>

#include "main.h"
#include "inc_def.h"		// Our own defines
#include "inc_startup.h"	// Startup Funkctions
#include "inc_uart.h"		// UART Handler functions
#include "inc_dspin.h"		// SPI Handler functions
#include "inc_lcd.h"		// LCD handler functions
#include "inc_msg.h"		// Protocol support
#include "inc_circular.h"	// Circular Buffer
#include "inc_motor.h"		// Motor handler functions

#endif

/* Global definierte Ringpuffer, da wir sie sowohl in der Main als auch im ISR-Handler brauchen (keine Übergabewerte */
Circ_Buf Ringpuffer_RX;
Circ_Buf Ringpuffer_TX;


//////////////////////////////////////////////////////////////////////////////////////////////////////////
////////////////////////////////    UART ISR	//////////////////////////////////////////
//////////////////////////////////////////////////////////////////////////////////////////////////////////

void UARTIntHandler(void){
	uint32_t ui32Status;
	uint8_t  c;

	ui32Status = UARTIntStatus(UART0_BASE, true);
	UARTIntClear(UART0_BASE, ui32Status);

	if((ui32Status & UART_INT_TX) || (eState.SER & SER_TX_REQUEST)){    	// auf Transmit Interrupt abfragen

		c = getChar(&Ringpuffer_TX);
		while(c != EXIT_BUFFER_EMPTY){			//prüfen auf fehlerbedingunng
			UARTCharPut(UART0_BASE, c);			//Zeichen in FIFO schieben
			c = getChar(&Ringpuffer_TX);
		}
		ui32Status ^= UART_INT_TX;
		eState.SER ^= SER_TX_REQUEST;
		GOTO_STATE(STATE_IDLE);
		//Finished with transmission
	}

	if((ui32Status & UART_INT_RX) || (ui32Status & UART_INT_RT)){

		while(UARTCharsAvail(UART0_BASE)){
			c = UARTCharGet(UART0_BASE);
			if(putChar(&Ringpuffer_RX, c) == EXIT_BUFFER_FULL){

				//We have had some kind of undetected buffer overflow
				eState.SER |= SER_RX_BUFFER_OVERRUN;
				GOTO_STATE(STATE_ERROR);

				//In the error state we will have to scan for remaining messages
				//and flush the buffer then!

			}

			if(c == '\n'){
				//We have a valid message! Do something about it!
				eState.SER |= SER_RX_MESSAGE_COMPLETE;
				GOTO_STATE(STATE_UART_COM);
			}
		}
		/* Empfang Vollständig - softwareflags Löschen */
		ui32Status &= !UART_INT_RX;
		ui32Status &= !UART_INT_RT;
	}

	if(ui32Status &  UART_INT_OE){
		ui32Status ^= UART_INT_OE;
		eState.SER |= SER_RX_ERROR;
	}

	if(ui32Status & UART_INT_BE){
		ui32Status ^= UART_INT_BE;
		eState.SER |= SER_RX_ERROR;
	}

	if(ui32Status & UART_INT_PE){
		ui32Status ^= UART_INT_PE;
		eState.SER |= SER_RX_ERROR;
	}

	if(ui32Status & UART_INT_FE){
		ui32Status ^= UART_INT_FE;
		eState.SER |= SER_RX_ERROR;
	}

	if(ui32Status != 0){
		GOTO_STATE(STATE_ERROR);
	}
}


/* Init_Transmission Startet den Sendevorgang über die UART-Schnittstelle
 * schnelle Dörte Lösung, aber es funktioniert
 */
void Init_Transmission(Circ_Buf *Buf){
	uint8_t c;
	c = getChar(Buf);
	if(c != EXIT_BUFFER_EMPTY)
		UARTCharPut(UART0_BASE, c);

	/* das programm läuft einmal "zu oft" in Init_Transmission - das nutzen wir hier aus, um den Idle-State aufzurufen */
	else GOTO_STATE(STATE_IDLE);
}


/* insertString dient als Wrapper-Funktion um einen String in send[128] einzufügen
 * die if-abfrage zu Beginn überprüft, ab wo platz zum schreiben ist
 */
uint32_t insertString(uint8_t str[128], uint8_t buf[128]){
	uint8_t i = 0;
	uint8_t ii = 0;

	while(str[ii] != 0)
		ii++;


	for(i = 0; i < 128; i++){
		*(str + ii + i) = buf[i];
	}
	return EXIT_SUCCESS;
}


/* clearString ist eine Wrapper-Funktion dessen zweck das löschen von send[128] ist */
uint32_t clearString(uint8_t str[128]){
	uint8_t i = 0;
	for(i = 0; i < 128; i++){
		str[i] = 0;
	}
	return EXIT_SUCCESS;
}

//////////////////////////////////////////////////////////////////////////////////////////////////////////
////////////////////////////////    Main	//////////////////////////////////////////
//////////////////////////////////////////////////////////////////////////////////////////////////////////


int main(void) {
	uint32_t i;
	uint32_t ii=0;
	sJob JobBuffer;
	sJob CurrentJob;
	uint8_t MsgPuffer[128];
	uint8_t send [128];
	uint16_t BufSize = 256;
	sJobQueue Job_Queue;
	uint32_t retVal;

	GOTO_STATE(STATE_STARTUP);

	while(1){

		////////////////// 	State Machine	////////////////////
		switch(SYS_STATE) {

		case STATE_STARTUP:
			SysCtlClockSet(SYSCTL_SYSDIV_4|SYSCTL_USE_PLL|SYSCTL_XTAL_16MHZ|SYSCTL_OSC_MAIN);
			setup_GPIO();
			setup_UART();
			setup_SPI();
			setup_INT();
			setup_HOME_POS();
			setup_JOB_QUEUE(&Job_Queue);

			jobDone(&CurrentJob);
			jobDone(&JobBuffer);

			clearString(send);
			clearString(MsgPuffer);

			Ringpuffer_RX.rdptr = BUF_SIZE - 1;
			Ringpuffer_RX.wrptr = 0;
			Ringpuffer_RX.size = BUF_SIZE;

			Ringpuffer_TX.rdptr = BUF_SIZE - 1;
			Ringpuffer_TX.wrptr = 0;
			Ringpuffer_TX.size = BUF_SIZE;

			GOTO_STATE(STATE_IDLE);
			break;


		case STATE_ERROR:

			switch (eState.SER){
			case SER_RX_TIMEOUT:

				insertString(send, (uint8_t*)" SER_RX_TIMEOUT ");
				insertString(send, (uint8_t*)" NACK ");
				eState.SER |= SER_TX_REQUEST;
				GOTO_STATE(STATE_UART_COM);
				eState.SER ^= SER_RX_TIMEOUT;
				clearString(send);
				for(i=0; i < 125; i++)
					*(send+i) = 0;
				break;

			case SER_RX_IDLE:
				insertString(send, (uint8_t*)" SER_RX_IDLE ");
				insertString(send, (uint8_t*)" NACK ");
				putMsg(&Ringpuffer_TX, send);
				eState.SER |= SER_TX_REQUEST;
				GOTO_STATE(STATE_UART_COM);
				eState.SER ^= SER_RX_IDLE;
				clearString(send);
				break;

			case SER_RX_ERROR:
				/* Dekodieren fehlgeschlagen, NACK senden */
				insertString(send, (uint8_t*)" SER_RX_ERROR ");
				insertString(send, (uint8_t*)" NACK ");
				putMsg(&Ringpuffer_TX, send);
				eState.SER |= SER_TX_REQUEST;
				GOTO_STATE(STATE_UART_COM);
				eState.SER ^= SER_RX_ERROR;
				clearString(send);
				break;

			case SER_TX_ERROR:
				insertString(send, (uint8_t*)" SER_TX_ERROR ");
				insertString(send, (uint8_t*)" NACK ");
				putMsg(&Ringpuffer_TX, send);
				eState.SER |= SER_TX_REQUEST;
				GOTO_STATE(STATE_UART_COM);
				eState.SER ^= SER_TX_ERROR;
				clearString(send);
				break;

			case SER_RX_BUFFER_OVERRUN:
				insertString(send, (uint8_t*)" SER_RX_BUFFER_OVERRUN ");
				insertString(send, (uint8_t*)" NACK ");
				putMsg(&Ringpuffer_TX, send);
				eState.SER |= SER_TX_REQUEST;
				GOTO_STATE(STATE_UART_COM);
				eState.SER ^= SER_RX_BUFFER_OVERRUN;
				clearString(send);
				break;

			case SER_RX_BUFFER_EMPTY:
				insertString(send, (uint8_t*)" SER_RX_BUFFER_EMPTY ");
				insertString(send, (uint8_t*)" NACK ");
				putMsg(&Ringpuffer_TX, send);
				eState.SER |= SER_TX_REQUEST;
				GOTO_STATE(STATE_UART_COM);
				eState.SER ^= SER_RX_BUFFER_EMPTY;
				clearString(send);
				break;

			default:
				break;
			}

			switch (eState.STA) {
			default:
				break;
			}

			switch (eState.ETH){
			default:
				break;
			}

			switch (eState.MSG){
			case MSG_LENGTH_ERROR:
				// Nachricht zu lang, bzw. Puffer voll
				insertString(send, (uint8_t*)" MSG_LENGTH_ERROR ");
				insertString(send, (uint8_t*)" NACK ");
				putMsg(&Ringpuffer_TX, send);
				eState.SER |= SER_TX_REQUEST;
				GOTO_STATE(STATE_UART_COM);
				eState.MSG ^= MSG_LENGTH_ERROR;
				clearString(send);
				break;

			case MSG_INVALID:
				// Nachriten-inhalt fehlerhaft
				insertString(send, (uint8_t*)" MSG_INVALID ");
				insertString(send, (uint8_t*)" NACK ");
				putMsg(&Ringpuffer_TX, send);
				eState.SER |= SER_TX_REQUEST;
				GOTO_STATE(STATE_UART_COM);
				eState.MSG ^= MSG_INVALID;
				clearString(send);
				break;

			case MSG_ID_ERROR:
				// Nachriten-ID fehlerhaft
				insertString(send, (uint8_t*)" MSG_ID_ERROR ");
				insertString(send, (uint8_t*)" NACK ");
				putMsg(&Ringpuffer_TX, send);
				eState.SER |= SER_TX_REQUEST;
				GOTO_STATE(STATE_UART_COM);
				eState.MSG ^= MSG_ID_ERROR;
				clearString(send);
				break;

			case MSG_CRC_ERROR:
				// CRC-Fehler
				insertString(send, (uint8_t*)" MSG_ID_ERROR ");
				insertString(send, (uint8_t*)" NACK ");
				putMsg(&Ringpuffer_TX, send);
				eState.SER |= SER_TX_REQUEST;
				GOTO_STATE(STATE_UART_COM);
				eState.MSG ^= MSG_CRC_ERROR;
				clearString(send);
				break;

			case MSG_CODE_ERROR:
				// Fehler im Coderahmen
				insertString(send, (uint8_t*)" MSG_CODE_ERROR ");
				insertString(send, (uint8_t*)" NACK ");
				putMsg(&Ringpuffer_TX, send);
				eState.SER |= SER_TX_REQUEST;
				GOTO_STATE(STATE_UART_COM);
				eState.MSG ^= MSG_CODE_ERROR;
				clearString(send);
				break;

			case MSG_UNKNOWN_ERROR:
				// Unbekannter Fehler
				insertString(send, (uint8_t*)" MSG_UNKNOWN_ERROR ");
				insertString(send, (uint8_t*)" NACK ");
				putMsg(&Ringpuffer_TX, send);
				eState.SER |= SER_TX_REQUEST;
				GOTO_STATE(STATE_UART_COM);
				eState.MSG ^= MSG_UNKNOWN_ERROR;
				clearString(send);
				break;

			default:
				break;
			}

			switch (eState.MOT){
			default:

				break;
			}

			switch (eState.JOB){
			case JOB_ADD_ERROR:

				insertString(send, (uint8_t*)" JOB_ADD_ERROR ");
				insertString(send, (uint8_t*)" NACK ");
				putMsg(&Ringpuffer_TX, send);
				eState.JOB ^= JOB_ADD_ERROR;
				eState.SER |= SER_TX_REQUEST;
				GOTO_STATE(STATE_UART_COM);
				clearString(send);
				break;

			case JOB_UNKNOWN_ERROR:
				insertString(send, (uint8_t*)" JOB_UNKNOWN_ERROR ");
				insertString(send, (uint8_t*)JobBuffer.id);
				insertString(send, (uint8_t*)" NACK ");
				putMsg(&Ringpuffer_TX, send);
				eState.JOB ^= JOB_UNKNOWN_ERROR;
				eState.SER |= SER_TX_REQUEST;
				GOTO_STATE(STATE_UART_COM);
				jobDone(&JobBuffer);
				clearString(send);
				break;

			default:
				break;
			}
			break;

			case STATE_JOB_HANDLING:

				if(eState.JOB & JOB_ADD_PENDING){
					/* Job zur Warteschlange hinzufügen und auf Erfolg Überprüfen,
					 * und Abarbeitung bzw. Fehlerbehandlung einleiten
					 */
					retVal = addJob(&Job_Queue, &JobBuffer);

					if(retVal == EXIT_SUCCESS){
						insertString(send, (uint8_t*)" JOB_ADD_SUCCESS ");
						insertString(send, (uint8_t*)JobBuffer.id);
						putMsg(&Ringpuffer_TX, send);
						clearString(send);
						jobDone(&JobBuffer);
						eState.SER |= SER_TX_REQUEST;
						GOTO_STATE(STATE_UART_COM);
					}
					else{
						eState.JOB |= JOB_ADD_ERROR;
						GOTO_STATE(STATE_ERROR);
					}
					eState.JOB ^= JOB_ADD_PENDING;
				}
				else GOTO_STATE(STATE_IDLE);

				break;

			case STATE_MSG_HANDLING:

				if(eState.SER & SER_RX_DECODE_VALID_MSG){
					retVal = decodeMsg(&Job_Queue, &JobBuffer, MsgPuffer);

					clearString(MsgPuffer);
					eState.SER ^= SER_RX_DECODE_VALID_MSG;

					switch (retVal){
					case MSG_ALL_OK:
						eState.JOB |= JOB_ADD_PENDING;
						GOTO_STATE(STATE_JOB_HANDLING);
						break;

					case MSG_INVALID:
						eState.MSG |= MSG_INVALID;
						GOTO_STATE(STATE_ERROR);
						break;

					case MSG_CRC_ERROR:
						eState.MSG |= MSG_CRC_ERROR;
						GOTO_STATE(STATE_ERROR);
						break;

					case MSG_ID_ERROR:
						eState.MSG |= MSG_ID_ERROR;
						GOTO_STATE(STATE_ERROR);
						break;

					case MSG_CODE_ERROR:
						eState.MSG |= MSG_CODE_ERROR;
						GOTO_STATE(STATE_ERROR);
						break;

					default:
						eState.MSG |= MSG_UNKNOWN_ERROR;
						GOTO_STATE(STATE_ERROR);
						break;
					}
				}
				else GOTO_STATE(STATE_IDLE);
				retVal=0;
				break;


			case STATE_UART_COM:

				if(eState.SER & SER_RX_MESSAGE_COMPLETE){
					retVal = getMsg(&Ringpuffer_RX, MsgPuffer, BufSize);

					switch(retVal){
					case EXIT_SUCCESS:
						GOTO_STATE(STATE_MSG_HANDLING);
						eState.SER |= SER_RX_DECODE_VALID_MSG;
						break;

					case EXIT_BUFFER_SIZE:
						eState.SER |= MSG_LENGTH_ERROR;
						GOTO_STATE(STATE_ERROR);
						break;

					case EXIT_BUFFER_EMPTY:
						eState.SER |= SER_RX_BUFFER_EMPTY;
						GOTO_STATE(STATE_ERROR);
						break;

					default:
						eState.SER |= SER_UNDEFINED_ERROR;
						GOTO_STATE(STATE_ERROR);
						break;
					}
					eState.SER ^= SER_RX_MESSAGE_COMPLETE;	// Flag Löschen
				}

				if(eState.SER & SER_TX_REQUEST){
					//Init_Transmission startet das Senden der UART schnittstelle
					Init_Transmission(&Ringpuffer_TX);
				}
				retVal = 0;
				break;


			case STATE_MOT_COM:

				/* Je Nach opCode wird eine entsprechende aktion ausgeführt */
				switch (CurrentJob.opCode){

				case (OPC_AUSGABE || OPC_NACHFUELLEN):
					/* Ein- und Ausgabe - "Normalbetrieb" */
					Ctrl_Motor(&CurrentJob);
					break;


				case OPC_FERNSTEUERN:
					/* Für "Manuelle" Steuerung der Motoren:
					 * "DEMO"/Test -Modus */
					Remote_Ctrl_Motor(&CurrentJob);
					break;

				case OPC_REKALIBRIEREN:
					/* Für die Änderung der Kästchenbreite, derzeit noch über defines gelöst */
					break;

				default:
					/* Irgendwas ist schiefgelaufen: id, fehlercode, NACK senden, Job löschen - Fehlersuche einbauen? */
					eState.JOB |= JOB_UNKNOWN_ERROR;
					GOTO_STATE(STATE_ERROR);
					break;
				}
				/* Nachricht an die höherstehende Logik, dass Job Ausgeführt wurde
				 * hierzu übertragen wir die ID des Jobs und enden mit ACK, bzw NACK
				 * letzteres ist allerdings noch nicht Implementiert für die Motorsteuerung
				 */
				if(eState.JOB ^ JOB_UNKNOWN_ERROR){
					insertString(send, (uint8_t*)" JOB_DONE ");
					insertString(send, (uint8_t*)CurrentJob.id);
					insertString(send, (uint8_t*)" ACK ");
					putMsg(&Ringpuffer_TX, send);
					eState.SER |= SER_TX_REQUEST;
					clearString(send);

					GOTO_STATE(STATE_UART_COM);
				}
				else{
					insertString(send, (uint8_t*)" JOB_UNKNOWN_ERROR ");
					insertString(send, (uint8_t*)CurrentJob.id);
					insertString(send, (uint8_t*)" NACK");
					putMsg(&Ringpuffer_TX, send);
					eState.SER |= SER_TX_REQUEST;

					clearString(send);

					GOTO_STATE(STATE_UART_COM);
				}
				jobDone(&CurrentJob);
				break;


				case STATE_NET_COM:
					break;


				case STATE_IDLE:
					// *Queue hat irgendein schrott drin stehn - warum?
					retVal = callJob(&Job_Queue, &CurrentJob);

					switch (retVal){
					case EXIT_SUCCESS:
						GOTO_STATE(STATE_MOT_COM);
						break;

					case JOB_PENDING:
						/* eventuelle Problembehandlung hier einfügen ??? */
						GOTO_STATE(STATE_MOT_COM);
						break;

						/*	case EXIT_FAILURE:
						 Warteschlange ist leer, ERROR-state aufrufen und und
						 * Nachsehen, ob noch Errorflags auf abhandlung warten

						GOTO_STATE(STATE_ERROR);
						break; */

					default:
						ii++;
						if(ii >= 150000){

							insertString(send, (uint8_t*)" IDLE ");
							putMsg(&Ringpuffer_TX, send);
							eState.SER |= SER_TX_REQUEST;
							clearString(send);
							ii = 0;
							GOTO_STATE(STATE_UART_COM);
						}
						retVal = 0;
						break;
					}



					//		 GPIOPinWrite(GPIO_PORTF_BASE, GPIO_PIN_1 | GPIO_PIN_2 | GPIO_PIN_3, GPIO_PIN_1);
					//		 SysCtlDelay(160000);
					//		 GPIOPinWrite(GPIO_PORTF_BASE, GPIO_PIN_1 | GPIO_PIN_2 | GPIO_PIN_3, GPIO_PIN_2);
					//		 SysCtlDelay(160000);


					break;
		}
	}
}

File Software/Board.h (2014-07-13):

/*
 * Copyright (c) 2014, Texas Instruments Incorporated
 * All rights reserved.
 *
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
 * *  Redistributions of source code must retain the above copyright
 *    notice, this list of conditions and the following disclaimer.
 *
 * *  Redistributions in binary form must reproduce the above copyright
 *    notice, this list of conditions and the following disclaimer in the
 *    documentation and/or other materials provided with the distribution.
 *
 * *  Neither the name of Texas Instruments Incorporated nor the names of
 *    its contributors may be used to endorse or promote products derived
 *    from this software without specific prior written permission.
 *
 * THIS SOFTWARE IS PROVIDED BY THE COPYRIGHT HOLDERS AND CONTRIBUTORS "AS IS"
 * AND ANY EXPRESS OR IMPLIED WARRANTIES, INCLUDING, BUT NOT LIMITED TO,
 * THE IMPLIED WARRANTIES OF MERCHANTABILITY AND FITNESS FOR A PARTICULAR
 * PURPOSE ARE DISCLAIMED. IN NO EVENT SHALL THE COPYRIGHT OWNER OR
 * CONTRIBUTORS BE LIABLE FOR ANY DIRECT, INDIRECT, INCIDENTAL, SPECIAL,
 * EXEMPLARY, OR CONSEQUENTIAL DAMAGES (INCLUDING, BUT NOT LIMITED TO,
 * PROCUREMENT OF SUBSTITUTE GOODS OR SERVICES; LOSS OF USE, DATA, OR PROFITS;
 * OR BUSINESS INTERRUPTION) HOWEVER CAUSED AND ON ANY THEORY OF LIABILITY,
 * WHETHER IN CONTRACT, STRICT LIABILITY, OR TORT (INCLUDING NEGLIGENCE OR
 * OTHERWISE) ARISING IN ANY WAY OUT OF THE USE OF THIS SOFTWARE,
 * EVEN IF ADVISED OF THE POSSIBILITY OF SUCH DAMAGE.
 */

#ifndef __BOARD_H
#define __BOARD_H

#ifdef __cplusplus
extern "C" {
#endif

#include "EK_TM4C123GXL.h"

#define Board_initDMA               EK_TM4C123GXL_initDMA
#define Board_initGeneral           EK_TM4C123GXL_initGeneral
#define Board_initGPIO              EK_TM4C123GXL_initGPIO
#define Board_initI2C				EK_TM4C123GXL_initI2C
#define Board_initSDSPI             EK_TM4C123GXL_initSDSPI
#define Board_initSPI               EK_TM4C123GXL_initSPI
#define Board_initUART              EK_TM4C123GXL_initUART
#define Board_initUSB               EK_TM4C123GXL_initUSB
#define Board_initWatchdog          EK_TM4C123GXL_initWatchdog
#define Board_initWiFi              EK_TM4C123GXL_initWiFi

#define Board_LED_ON                EK_TM4C123GXL_LED_ON
#define Board_LED_OFF               EK_TM4C123GXL_LED_OFF
#define Board_LED0                  EK_TM4C123GXL_LED_BLUE
#define Board_LED1                  EK_TM4C123GXL_LED_GREEN
#define Board_LED2                  EK_TM4C123GXL_LED_RED
#define Board_BUTTON0               EK_TM4C123GXL_SW1
#define Board_BUTTON1               EK_TM4C123GXL_SW2

#define Board_I2C0                  EK_TM4C123GXL_I2C0
#define Board_I2C1                  EK_TM4C123GXL_I2C3
#define Board_I2C_TMP               EK_TM4C123GXL_I2C3
#define Board_I2C_NFC               EK_TM4C123GXL_I2C3
#define Board_I2C_TPL0401           EK_TM4C123GXL_I2C3

#define Board_SDSPI0                EK_TM4C123GXL_SDSPI0

#define Board_SPI0                  EK_TM4C123GXL_SPI0
#define Board_SPI1                  EK_TM4C123GXL_SPI3
#define Board_SPI_CC3000            EK_TM4C123GXL_SPI2

#define Board_USBDEVICE             EK_TM4C123GXL_USBDEVICE

#define Board_UART0                 EK_TM4C123GXL_UART0

#define Board_WATCHDOG0             EK_TM4C123GXL_WATCHDOG0

#define Board_WIFI                  EK_TM4C123GXL_WIFI

#define Board_gpioCallbacks0        EK_TM4C123GXL_gpioPortFCallbacks
#define Board_gpioCallbacks1        EK_TM4C123GXL_gpioPortFCallbacks

/* Board specific I2C addresses */
#define Board_TMP006_ADDR           (0x40)
#define Board_RF430CL330_ADDR       (0x28)
#define Board_TPL0401_ADDR          (0x40)

#ifdef __cplusplus
}
#endif

#endif /* __BOARD_H */

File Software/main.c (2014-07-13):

/*
 * Copyright (c) 2014, Texas Instruments Incorporated
 * All rights reserved.
 *
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
 * *  Redistributions of source code must retain the above copyright
 *    notice, this list of conditions and the following disclaimer.
 *
 * *  Redistributions in binary form must reproduce the above copyright
 *    notice, this list of conditions and the following disclaimer in the
 *    documentation and/or other materials provided with the distribution.
 *
 * *  Neither the name of Texas Instruments Incorporated nor the names of
 *    its contributors may be used to endorse or promote products derived
 *    from this software without specific prior written permission.
 *
 * THIS SOFTWARE IS PROVIDED BY THE COPYRIGHT HOLDERS AND CONTRIBUTORS "AS IS"
 * AND ANY EXPRESS OR IMPLIED WARRANTIES, INCLUDING, BUT NOT LIMITED TO,
 * THE IMPLIED WARRANTIES OF MERCHANTABILITY AND FITNESS FOR A PARTICULAR
 * PURPOSE ARE DISCLAIMED. IN NO EVENT SHALL THE COPYRIGHT OWNER OR
 * CONTRIBUTORS BE LIABLE FOR ANY DIRECT, INDIRECT, INCIDENTAL, SPECIAL,
 * EXEMPLARY, OR CONSEQUENTIAL DAMAGES (INCLUDING, BUT NOT LIMITED TO,
 * PROCUREMENT OF SUBSTITUTE GOODS OR SERVICES; LOSS OF USE, DATA, OR PROFITS;
 * OR BUSINESS INTERRUPTION) HOWEVER CAUSED AND ON ANY THEORY OF LIABILITY,
 * WHETHER IN CONTRACT, STRICT LIABILITY, OR TORT (INCLUDING NEGLIGENCE OR
 * OTHERWISE) ARISING IN ANY WAY OUT OF THE USE OF THIS SOFTWARE,
 * EVEN IF ADVISED OF THE POSSIBILITY OF SUCH DAMAGE.
 */

/*
 *  ======== empty.c ========
 */

#include <stdio.h>
#include <stdlib.h>
#include <cstring>
/* XDCtools Header files */
#include <xdc/std.h>
#include <xdc/cfg/global.h>
#include <xdc/runtime/System.h>

/* BIOS Header files */
#include <ti/sysbios/BIOS.h>
#include <ti/sysbios/knl/Semaphore.h>

/* TI-RTOS Header files */
#include <ti/drivers/GPIO.h>
// #include <ti/drivers/I2C.h>
// #include <ti/drivers/SPI.h>
#include <ti/drivers/UART.h>
// #include <ti/drivers/Watchdog.h>
// #include <ti/drivers/WiFi.h>

/* Board Header file */
#include "Board.h"



void FXN_uart_callback(UART_Handle handle, void *buf, int count);

UART_Params uartParams;	// Parameter struct for UART0
UART_Handle uart;		// UART driver handle
uint8_t uartRxBuf[256];
#define UART_NEWLINE 	 "\n"
#define UART_CMDLINE 	 "~: "


/*
 *  ======== heartBeatFxn ========
 *  Toggle the Board_LED0. The Task_sleep is determined by arg0 which
 *  is configured for the heartBeat Task instance.
 */
Void TSK_heartBeatFxn(UArg arg0, UArg arg1)
{
	UART_write(uart, UART_CMDLINE, sizeof(UART_CMDLINE) - 1);	// Print commandline
	UART_read(uart, uartRxBuf, sizeof(uartRxBuf));			// Read from the UART once to start a continuous read

    while (1) {
        Task_sleep((UInt)arg0);
        GPIO_toggle(Board_LED0);
	}
}

void TSK_handleUartRXFxn(UArg arg0, UArg arg1){
	uint16_t i 							= 0;
	uint8_t UART_NEWLINE_FOUND		 	= 0;
	uint8_t UART_NO_NEWLINE_PRESENT 	= 0;

	while(1){
		Semaphore_pend(sem_uart_rxdone, BIOS_WAIT_FOREVER);	// Wait for message to arrive

		i 							= 0;
		UART_NO_NEWLINE_PRESENT 	= 0;
		UART_NEWLINE_FOUND 			= 0;

		while(!UART_NEWLINE_FOUND && !UART_NO_NEWLINE_PRESENT){		// Prevent i from overflowing the buffer
			if(i >= sizeof(uartRxBuf)){
				UART_NO_NEWLINE_PRESENT = 1;
				#ifdef DEBUG
				System_printf("Error in UART Message handling: No newline character found!\n");
				System_flush();
				#endif
			}
			if(uartRxBuf[i] == '\n'){
				UART_NEWLINE_FOUND = 1;
			}
			else{
				i = i + 1;
			}
		}

		if(!UART_NO_NEWLINE_PRESENT && (uartRxBuf[0] != '\n')){
			// Parse
			//UART_write(uart, uartRxBuf, i);
			if(strcmp((char*)uartRxBuf , "SET RED LED ON\n")){
				 GPIO_write(Board_LED1,Board_LED_ON);
				 UART_write(uart, "RED LED IS ON",sizeof("RED LED IS ON"));
			}
			if(uartRxBuf == "SET RED LED OFF\n"){
				 GPIO_write(Board_LED1,Board_LED_OFF);
				 UART_write(uart, "RED LED IS OFF",sizeof("RED LED IS OFF"));
			}
			UART_write(uart, UART_NEWLINE, sizeof(UART_NEWLINE) - 1);
			UART_write(uart, UART_CMDLINE, sizeof(UART_CMDLINE) - 1);
			for(i = 0; i < sizeof(uartRxBuf);i++) uartRxBuf[i] = 0;
		}
		else{
			if(UART_NO_NEWLINE_PRESENT){
				System_printf("Error in UART Message handling: No Newline present!\n Buffer contents ' %s '\n",uartRxBuf);
				System_flush();
				UART_write(uart, UART_CMDLINE, sizeof(UART_CMDLINE) - 1);
			}
			for(i = 0; i < sizeof(uartRxBuf);i++) uartRxBuf[i] = 0;
		}
		UART_read(uart, uartRxBuf, sizeof(uartRxBuf));
	}
}



/*
 *  ======== main ========
 */
int main(void)
{
    /* Call board init functions */
    Board_initGeneral();
    Board_initGPIO();
    // Board_initDMA();
    // Board_initI2C();
    // Board_initSPI();
    Board_initUART();
    // Board_initUSB(Board_USBDEVICE);


    /* Initialize drivers */
    UART_Params_init(&uartParams);
    uartParams.readMode 		= UART_MODE_CALLBACK;
    uartParams.writeMode 		= UART_MODE_BLOCKING;
    uartParams.readCallback 	= &FXN_uart_callback;
    uartParams.writeDataMode 	= UART_DATA_BINARY;
    uartParams.readDataMode 	= UART_DATA_TEXT;
    uartParams.readReturnMode 	= UART_RETURN_NEWLINE;
    uartParams.readEcho	 		= UART_ECHO_OFF;
    uartParams.baudRate 		= 9600;
    uartParams.dataLength		= UART_LEN_8;
    uartParams.stopBits			= UART_STOP_ONE;
    uartParams.parityType		= UART_PAR_NONE;
    uart = UART_open(Board_UART0, &uartParams);

    /* SPI */

    /* Ethernet */

    /* End init drivers */

    /* Turn on user LED */
    GPIO_write(Board_LED0, Board_LED_ON);

    System_printf("Inits done. Starting BIOS\n");
    /* SysMin will only print to the console when you call flush or exit */
    System_flush();

    /* Start BIOS */
    BIOS_start();

    return (0);
}

void FXN_uart_callback(UART_Handle handle, void *buf, int count){
	Semaphore_post(sem_uart_rxdone);

}

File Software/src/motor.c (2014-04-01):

/*
 * motor.c
 *
 *  Created on: 21.11.2013
 *      Author: einball-dev
 */

#include "inc_motor.h"
#include "inc_dspin.h"




uint32_t getBox(sJob *Destination){

	/* Fahrtrichtung bestimmen und XY-Position Anfahren */

	if((((Destination->coordX + Offset_X) * Stepsize) - dSPIN_GetParam(MOT_X_AXIS_1, dSPIN_ABS_POS)) > 0){
		dSPIN_GoTo_DIR(MOT_X_AXIS_1, 1, (Destination->coordX + Offset_X) * Stepsize);
	}
	else{dSPIN_GoTo_DIR(MOT_X_AXIS_1, 0, (Destination->coordX + Offset_X) * Stepsize);}

	if((((Destination->coordY + Offset_Y) * Stepsize) - dSPIN_GetParam(MOT_Y_AXIS, dSPIN_ABS_POS)) > 0){
		dSPIN_GoTo_DIR(MOT_Y_AXIS, 1, (Destination->coordY + Offset_Y) * Stepsize);
	}
	else{dSPIN_GoTo_DIR(MOT_Y_AXIS, 0, (Destination->coordY + Offset_Y) * Stepsize);}


	while(1){
		if((1 & dSPIN_GetParam(MOT_X_AXIS_1, dSPIN_STATUS)) && (1 & dSPIN_GetParam(MOT_Y_AXIS, dSPIN_STATUS))){
			// Warten, bis X und Z Position angefahren wurden
			break;
		}
	}

	/* Greifer öffnen, Z-Position anfahren, Box greifen und rausziehen */
	dSPIN_GoTo(MOT_GRIPPER, Destination->GRIPPER * (BoxSize + Offset_GRIPPER) * Stepsize);
	while(1){
		if(1 & dSPIN_GetParam(MOT_GRIPPER, dSPIN_STATUS)){
			// Warten, bis Greifer geöffnet wurde
			break;
		}
	}

	dSPIN_GoTo(MOT_Z_AXIS, Destination->coordZ * BoxSize * Stepsize);
	while(1){
		if(1 & dSPIN_GetParam(MOT_Z_AXIS, dSPIN_STATUS)){
			// Warten, bis  Z Position angefahren wurde
			break;
		}
	}

	dSPIN_GoTo(MOT_GRIPPER, Destination->GRIPPER * BoxSize * Stepsize);
	while(1){
		if(1 & dSPIN_GetParam(MOT_GRIPPER, dSPIN_STATUS)){
			// Warten, bis Greifer geschlossen wurde
			break;
		}
	}

	dSPIN_GoHome(MOT_Z_AXIS);
	while(1){
		if(1 & dSPIN_GetParam(MOT_Z_AXIS, dSPIN_STATUS)){
			// Warten, bis  Z Position zurückgesetzt wurde
			break;
		}
	}
	return EXIT_SUCCESS;
}


uint32_t putBox(sJob *Destination){


	/* Fahrtrichtung bestimmen und XY-Position Anfahren */
	if((((Destination->coordX + Offset_X) * Stepsize) - dSPIN_GetParam(MOT_X_AXIS_1, dSPIN_ABS_POS)) >0){
		dSPIN_GoTo_DIR(MOT_X_AXIS_1, 1, (Destination->coordX + Offset_X) * Stepsize);
	}
	else{dSPIN_GoTo_DIR(MOT_X_AXIS_1, 0, (Destination->coordX + Offset_X) * Stepsize);}

	if((((Destination->coordY + Offset_Y) * Stepsize) - dSPIN_GetParam(MOT_Y_AXIS, dSPIN_ABS_POS)) >0){
		dSPIN_GoTo_DIR(MOT_Y_AXIS, 1, (Destination->coordY + Offset_Y) * Stepsize);
	}
	else{dSPIN_GoTo_DIR(MOT_Y_AXIS, 0, (Destination->coordY + Offset_Y) * Stepsize);}


	while(1){
		if((1 & dSPIN_GetParam(MOT_X_AXIS_1, dSPIN_STATUS)) && ( 1 &dSPIN_GetParam(MOT_Y_AXIS, dSPIN_STATUS))){
			// Warten, bis X und Y Position angefahren wurden
			break;
		}
	}


	/* Z-Position anfahren, Box ablegen und zurückfahren */

	dSPIN_GoTo(MOT_Z_AXIS, ((Destination->coordZ + Offset_Z) * Stepsize));
	while(1){
		if(1 & dSPIN_GetParam(MOT_Z_AXIS, dSPIN_STATUS)){
			// Warten, bis  Z Position angefahren wurde
			break;
		}
	}

	dSPIN_GoTo(MOT_GRIPPER, Destination->GRIPPER * (BoxSize + Offset_GRIPPER) * Stepsize); // Platzhalter für Greiferstellung
	while(1){
		if(1 & dSPIN_GetParam(MOT_GRIPPER, dSPIN_STATUS)){
			// Warten, bis Greifer geöffnet wurde
			break;
		}
	}

	dSPIN_GoHome(MOT_Z_AXIS);
	while(1){
		if(1 & dSPIN_GetParam(MOT_Z_AXIS, dSPIN_STATUS)){
			// Warten, bis  Z Position zurückgesetzt wurde
			break;
		}
	}

	return EXIT_SUCCESS;
}


uint32_t EmptyBox(){

	dSPIN_GoHome(MOT_X_AXIS_1);
	if(((AusgabeschachtY + Offset_Y) * Stepsize - dSPIN_GetParam(MOT_Y_AXIS, dSPIN_ABS_POS)) > 0){
		dSPIN_GoTo_DIR(MOT_Y_AXIS, 1, (AusgabeschachtY + Offset_Y) * Stepsize);
	}
	else{dSPIN_GoTo_DIR(MOT_Y_AXIS, 0, (AusgabeschachtY + Offset_Y) * Stepsize);}

	while(1){
		// Warten, bis X und Y Position angefahren wurden
		if((1 & dSPIN_GetParam(MOT_X_AXIS_1, dSPIN_STATUS)) && (1 & dSPIN_GetParam(MOT_Y_AXIS, dSPIN_STATUS))){
		break;
		}
	}

	dSPIN_GoTo(MOT_Z_AXIS, (AusgabeschachtZ + Offset_Z) * Stepsize);
	while(1){
		// Warten, bis  Z Position angefahren wurde
		if(1&dSPIN_GetParam(MOT_Z_AXIS, dSPIN_STATUS)){
		break;
		}
	}

	dSPIN_GoTo(MOT_JOINT, Halbkreis);
	while(1){
		if(1 & dSPIN_GetParam(MOT_JOINT, dSPIN_STATUS)){
			// Warten, bis fertig Rotiert
			break;
		}
	}
	dSPIN_GoHome(MOT_JOINT);
	dSPIN_GoHome(MOT_Z_AXIS);
	while(1){
		if(1 & dSPIN_GetParam(MOT_Z_AXIS, dSPIN_STATUS)){
			// Warten, bis  Z Position zurückgesetzt wurde
			break;
		}
	}

	return EXIT_SUCCESS;
}

uint32_t RefillBox(){

	dSPIN_GoHome(MOT_X_AXIS_1);
	if(((AusgabeschachtY + Offset_Y) * Stepsize - dSPIN_GetParam(MOT_Y_AXIS, dSPIN_ABS_POS)) > 0){
		dSPIN_GoTo_DIR(MOT_Y_AXIS, 1, (AusgabeschachtY + Offset_Y) * Stepsize);
	}
	else{dSPIN_GoTo_DIR(MOT_Y_AXIS, 0, (AusgabeschachtY + Offset_Y) * Stepsize);}

	while(1){
		if((1 & dSPIN_GetParam(MOT_X_AXIS_1, dSPIN_STATUS)) && (1 & dSPIN_GetParam(MOT_Y_AXIS, dSPIN_STATUS))){
			// Warten, bis X und Y Position angefahren wurden
			break;
		}
	}

	dSPIN_GoTo(MOT_Z_AXIS, (AusgabeschachtZ + Offset_Z) * Stepsize);
	while(1){
		//muss noch auf den richtigen Port/Pin abgestimmt werden, siehe auch: startup.c
		if(GPIOPinRead(GPIO_PORTF_BASE, GPIO_PIN_4))
			break;
	}

	dSPIN_GoHome(MOT_Z_AXIS);

	while(1){
		if(1 & dSPIN_GetParam(MOT_Z_AXIS, dSPIN_STATUS)){
			// Warten, bis  Z Position zurückgesetzt wurde
			break;
		}

	}

	return EXIT_SUCCESS;
}
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

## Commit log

2014-06-29 Version 2 der Elektronik hinzugefügt. Modularisiert. WIP!
    [Mainboard.brd, Mainboard.sch, Stepperdriver.brd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]
2014-07-13 Start der Umstellung auf das RTOS
    [BIOS.obj, build.cfg, dmtimer_Timer_asm.obj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]
2014-07-22 Elektronik auf den neusten Stand gebracht (Merge mit privater Dropbox
    [Mainboard.brd, Mainboard.sch, Stepperdriver.brd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]
2014-07-22 Stepperendstufe weitergeroutet
    [Stepperdriver.brd, Stepperdriver.sch]
2014-10-14 test commit
    [1.1.1.1.sldprt, 2.1.1.1.sldprt, 416-010-0014.SLDPRT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]
